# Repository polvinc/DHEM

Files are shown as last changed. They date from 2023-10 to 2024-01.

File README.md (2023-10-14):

# DHEM: another DIY Harmonic Equatorial Mount
## What the hell is this DHEM thing?

DHEM (DIY Harmonic Equatorial Mount) is an equatorial mount for observation or astrophotography. It is based on the use of a harmonic reducer. The mount is designed to be inexpensive in relation to its performance, transportable, with a relatively large load capacity. Most importantly, this mount is easy to build: no need for machine tools or other laser-cutting-water-jet-plasma-turbo-piston-5-axis machines. A shopping list, a screwdriver, a saw and some resourcefulness: you've got everything you need to make a DHEM. The ultimate aim is to distribute its design as an open-source product for personal use.

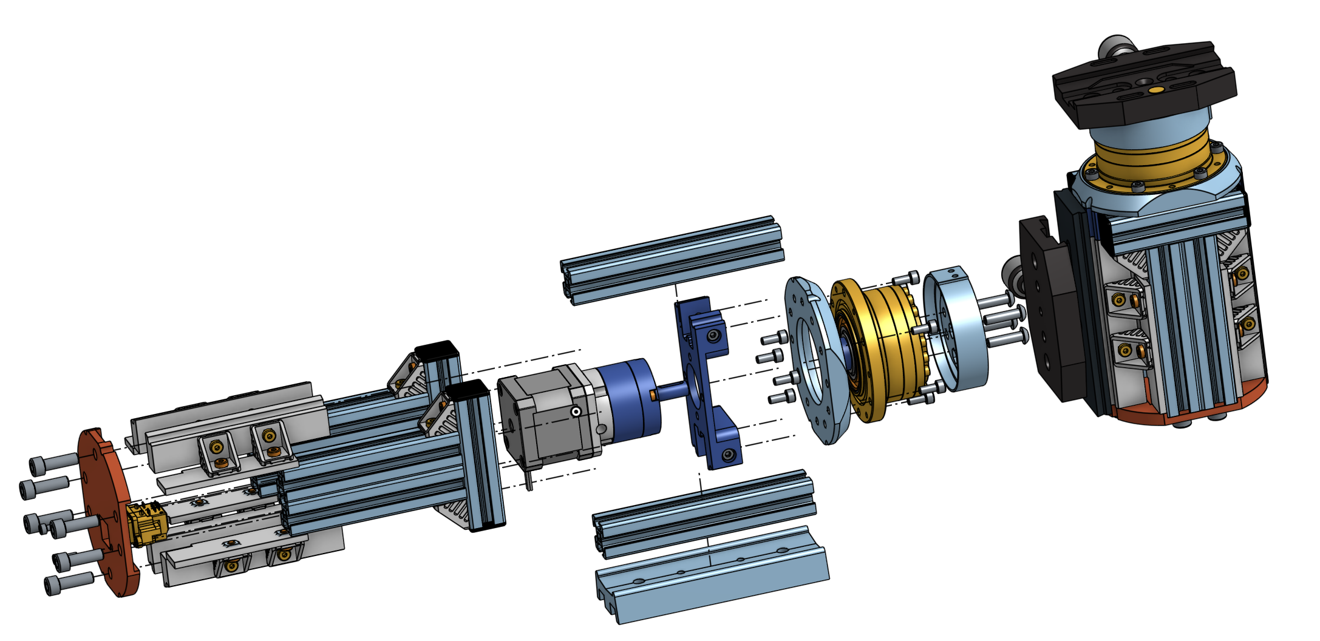
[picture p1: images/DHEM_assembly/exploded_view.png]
exploded_view


The technology used in this mount is similar to that used in robotics or industrial production lines. The main mechanical gearbox is a harmonic gearbox ([wikipedia](https://en.wikipedia.org/wiki/Strain_wave_gearing)). 



It can produce surprising results for an astronomical mount at first glance; the mount appears grossly undersized and unbalanced, whereas the whole assembly is extremely robust and stable, with enormous torque.
Conventional equatorial mounts require the use of counterweights. The aim of this development is to make available the design of a harmonic mount that can be built in your garage, with few tools or mechanical knowledge, for a price of less than 1000€. Of course, the proud aim is to achieve performance equivalent to that of commercial harmonic reduction mounts.

- Harmonic gear motor
- BOM less than 1000€
- No need for machine tools: all you need is a saw and a screwdriver!
- Lightweight: max 5 kg
- Minimum load weight without counterweight: > 12kg (to be tested)

The first results of the performance tests are up to my expectations for the moment. I hope this github repository can help you design or reproduce this equatorial mount. Please be patient, I'm only working on this project in my spare time. I'll update the testing progress on this readme. ✍️

## Support

Hey! Help me out for a couple of :beers: !

<a href="https://www.buymeacoffee.com/polvinc" target="_blank">Buy Me A Coffee</a>

# Design
## 3D design
The 3D design was carried out on SolidWorks 2022 and OnShape. Here's a [sharing of the design on OnShape](https://cad.onshape.com/documents/8746a60a1be674f3c5c8962f/w/75df6ccf1ddba0eb14d42c4d/e/8f9338159e7a1463ffcd3219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). The project is a bit of a mess, but it includes all the components needed to assemble the mount. You will find all stl files for printing in this repo.

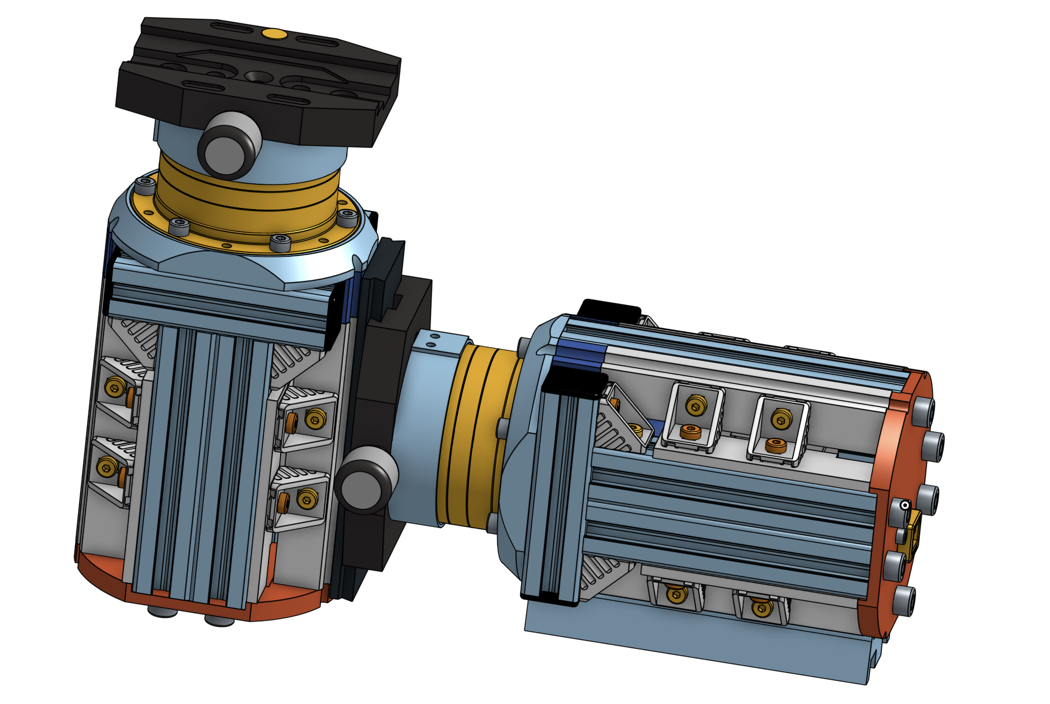
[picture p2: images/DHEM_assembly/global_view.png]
global_view


## Bill of materials
Here's the shopping list for two axes. Prices are approximate: I already had quite a few parts in stock when designing the DHEM. The total investment is around 900€ for the mechanics, and I estimate the cost of making an [OnStep](https://onstep.groups.io/g/main/wiki/Home) MiniPCB2 controller at 100€.

<b>The estimated total cost of the equatorial mount is less than 1000€</b>.

I think you can save a lot of money by going to other supply sites. For example, I got about €70 worth of Bosch M4 T-nuts from RS Components, when I could have got them for 5 or 10 times less with no-name ([for example](https://www.amazon.fr/EYPINS-Connecteur-Aluminium-28x28x20mm-dextrusion/dp/B08GPRB9W4/?th=1), [another example](https://www.amazon.fr/alwaiiz-aluminium-galvanisé-dextrusion-européenne/dp/B0B5GKW3MT/)). I had Bosch in my stuff, so I didn't deprive myself.

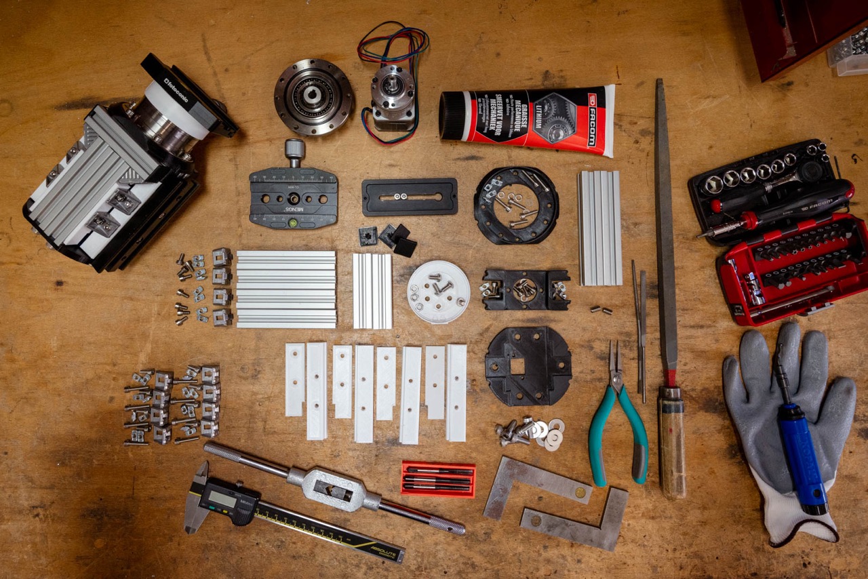
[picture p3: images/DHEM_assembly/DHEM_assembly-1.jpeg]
final_assembly_1


| Name | Quantity | Reference | Price € | Link |
| --- | --- | --- | --- | --- |
M4x8 | 32 | - | a few | 
M4x10 | 16 | - | a few | 
M4x16 | 20 | - | a few | 
M4x20 | 20 | - | a few | 
M5x10 | 8 | - | a few | 
M5x20 | 6 | - | a few | 
M6x16 | 12 | - | a few | 
20mm Bosch Rexroth profile | 1 | 212-3292 | 25 | [RS components](https://fr.rs-online.com/web/p/tubes-et-profiles-de-structures/2123292?gb=s)
T-nuts | 64 | 466-7281 | 70 | [RS components](https://fr.rs-online.com/web/p/raccords-pour-elements-de-structure/4667281)
M4 Angle Bracket | 24 | 180-9136 | 30 | [RS components](https://fr.rs-online.com/web/p/raccords-pour-elements-de-structure/1809136)
M4 inside M6 insert | 4 | B096VSWCBQ | 8 | [Amazon FR](https://www.amazon.fr/dp/B096VSWCBQ?psc=1&ref=ppx_yo2ov_dt_b_product_details)
Dovetail Clamp | 1 | EUF9144C | 30 | [Amazon FR](https://www.amazon.fr/gp/product/B08TC111QC/ref=ppx_yo_dt_b_search_asin_title?ie=UTF8&psc=1)
Dovetail Mounting Plate | 1 | EUF9175B | 20 | [Amazon FR](https://www.amazon.fr/gp/product/B08XLWP13X/ref=ppx_yo_dt_b_search_asin_title?ie=UTF8&psc=1)
Arca clamp | 1 | B0BW3SSHY1 | 20 | [Amazon FR](https://www.amazon.fr/QLOUNI-dégagement-Déclenchement-Appareil-Universelle/dp/B0BW3SSHY1/)
Arca mounting | 1 | B0771KW7TK | 15 | [Amazon FR](https://www.amazon.fr/gp/product/B0771KW7TK/ref=ppx_yo_dt_b_search_asin_title?ie=UTF8&th=1)
| Nema 17 with 10:1 Planetary Gearbox | 2 | 17HS15-1584S-MG10 | 60 | [StepperOnline](https://www.omc-stepperonline.com/fr/nema-17-moteur-pas-a-pas-l-40mm-rapport-de-vitesse-10-1-reducteur-planetaire-serie-mg-17hs15-1584s-mg10)
Harmonic Drive | 2 | CSF-17-100-2UH | 550 | [ebay](https://www.ebay.fr/sch/i.html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) ([datasheet](https://www.harmonicdrive.net/products/gear-units/gear-units/csf-2uh/csf-17-100-2uh))
RJ45 connector | 2 | MRJ5380M1 | 35 | [Farnell](https://fr.farnell.com/amphenol-communications-solutions/mrj5380m1/conn-rj45-90-jack-8p8c-1-port/dp/4122450)
OnStep controller | 1 | MiniPCB2 | ~100 | [oshwlab](https://oshwlab.com/hujer.roman/minipcb2)

# Assembly

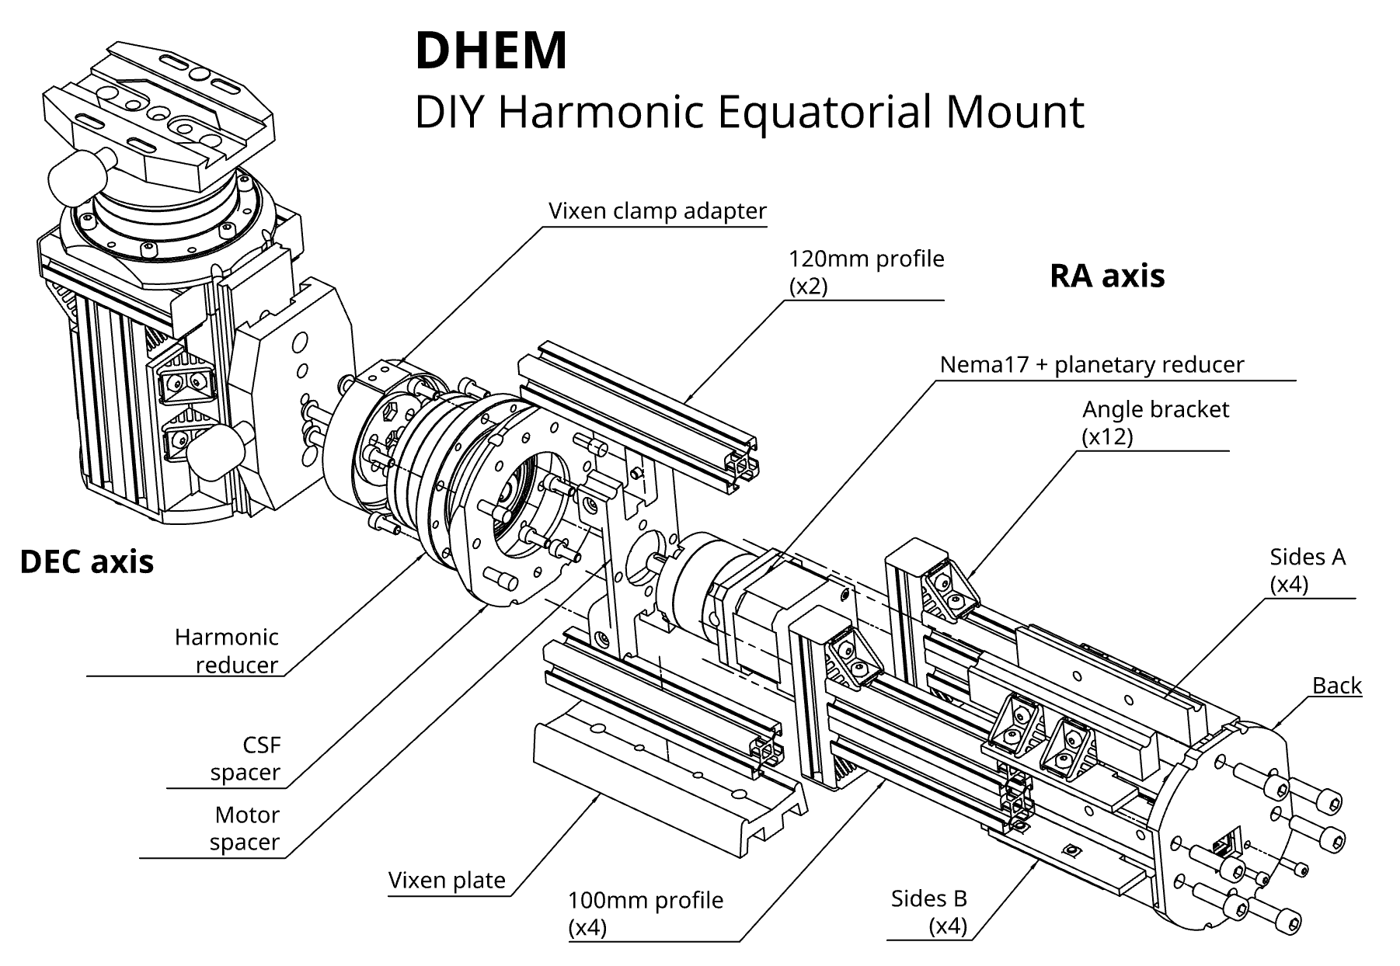
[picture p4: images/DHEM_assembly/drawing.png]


## Harmonic drive
Harmonic gearboxes ([wikipedia](https://en.wikipedia.org/wiki/Strain_wave_gearing)), or more precisely strain wave gears, are a type of gear mechanism that transmits much more torque than other common gears. This is mainly due to the fact that there are many more teeth engaged at once. One of the major advantages of these gears is that they have virtually no backlash, partly because they use deformation. It's a bit like belts, which are supposed to be more or less backlash-free, but harmonic gearboxes use deformable metal spring steels, which are much better than belts.

Put another way, in the case of an astronomical mount: they can drive much heavier loads without the need for counterweights, all with a very low self-weight!

<p align="center">
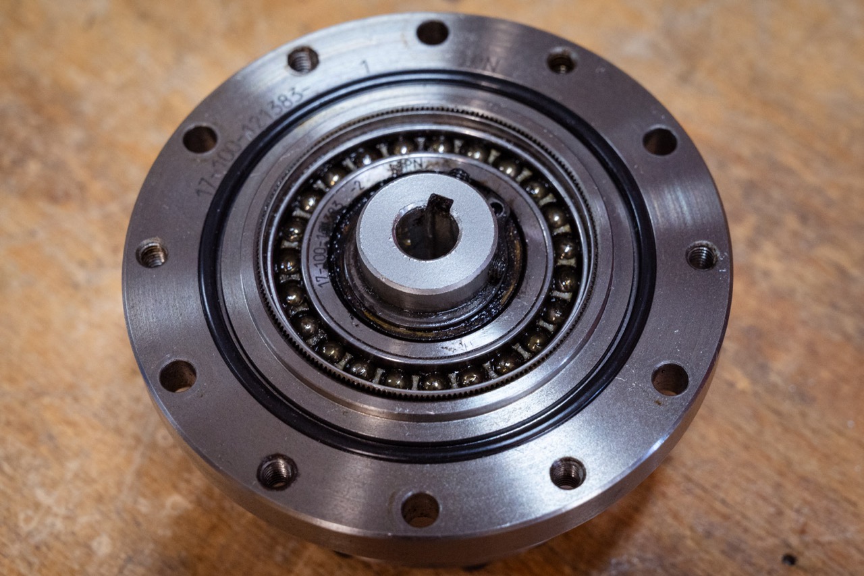
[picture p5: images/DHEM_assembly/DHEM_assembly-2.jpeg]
  
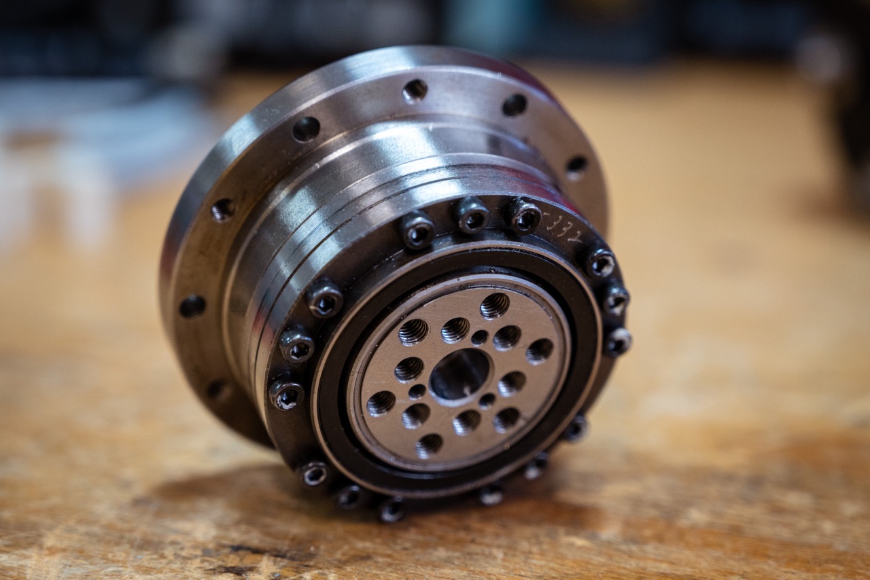
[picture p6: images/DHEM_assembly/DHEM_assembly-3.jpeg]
  
</p> 

The harmonic reducer model chosen [CSF-17-100-2UH](https://harmonicdrive.de/fileadmin/user_upload/Harmonic_Drive_Gears_EN_1050860_06_2022.pdf#page=50) is the same as [Alan](https://alanz.info/posts/2022/07/diy-mount/) DIY mount. You can find lots of them on ebay. This one has a reduction ratio of 1/100. It has the good fortune to meet my requirements, and to have been tested for another equatorial mount. Why deprive yourself? According to datasheet, it can handle more than 50Nm of torque and it also has a very comfortable permissible radial load of over 70Kg.
<p align="center">
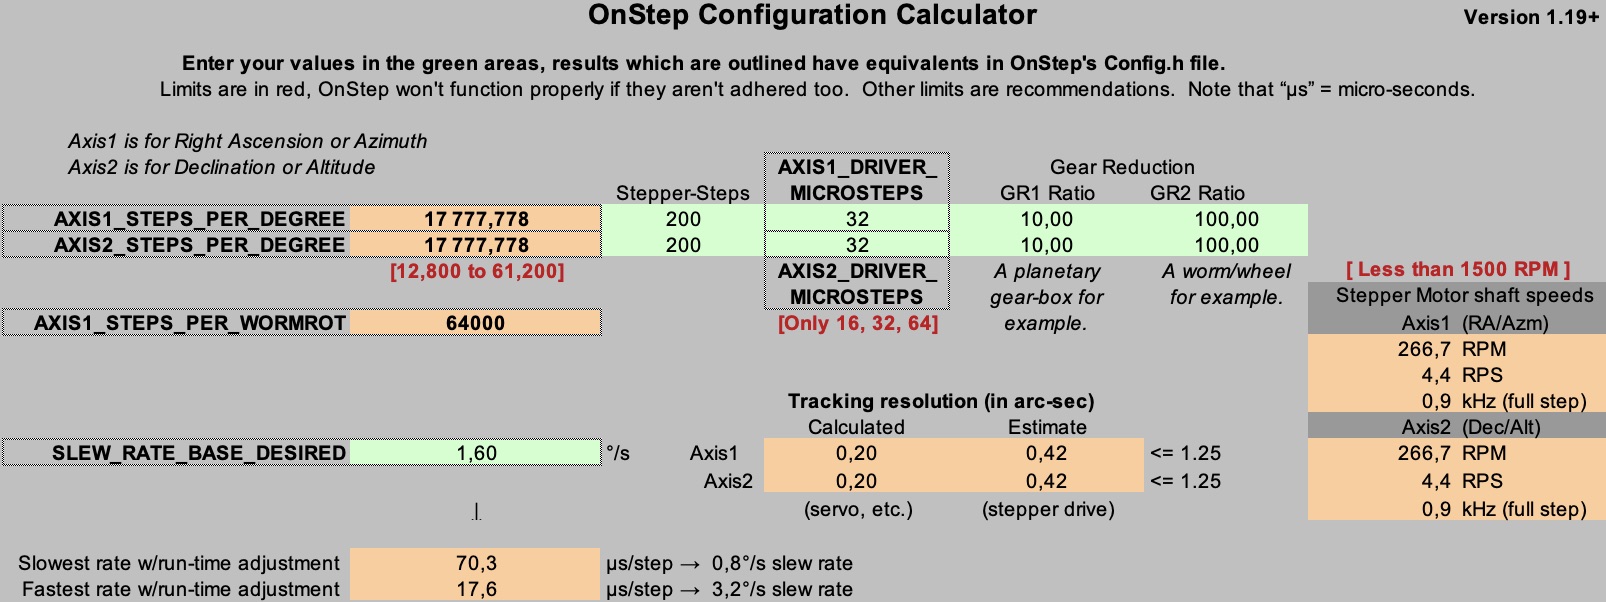
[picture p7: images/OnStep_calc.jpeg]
  
</p>

Using [OnStep's configurator spreadsheet](http://o.baheyeldin.com:1111), I chose to drive the harmonic gearbox with a planetary gearbox [17HS15-1584S-MG10](https://www.omc-stepperonline.com/fr/nema-17-moteur-pas-a-pas-l-40mm-rapport-de-vitesse-10-1-reducteur-planetaire-serie-mg-17hs15-1584s-mg10), in order to achieve good tracking resolution, a good slew rate and a good number of steps/deg. Its reduction ratio is 1/10 and it is given for a low backlash (around 30 arcmin). Seen through the telescope, this low backlash will be divided by 100 by the main gearbox. You can probably use another motor with a planetary gearbox.

<p align="center">
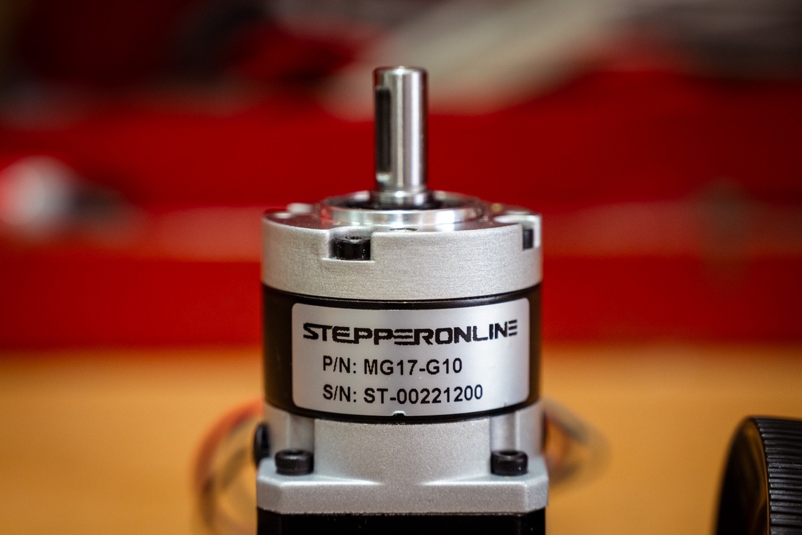
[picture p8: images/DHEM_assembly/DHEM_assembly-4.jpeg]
  
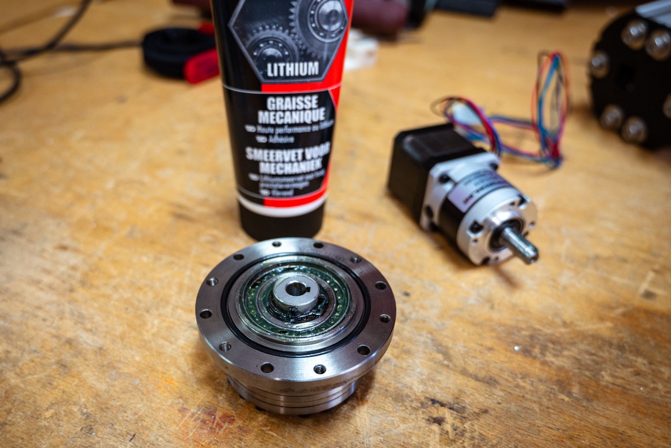
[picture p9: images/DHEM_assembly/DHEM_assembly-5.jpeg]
  
</p>

## Motor holding
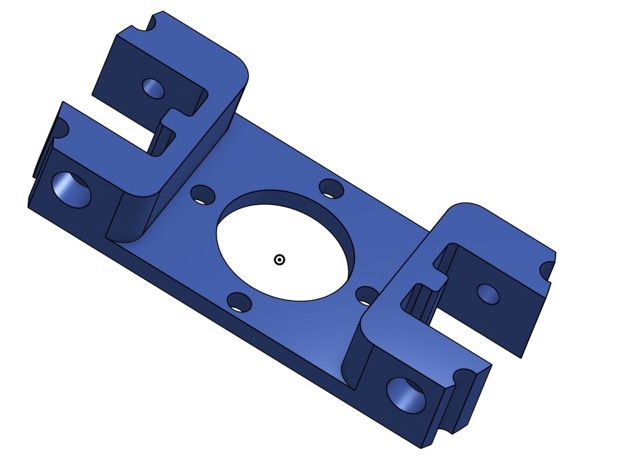
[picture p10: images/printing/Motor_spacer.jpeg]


We start assembling the mount, attaching the motor and its planet gear to the 3D-printed motor spacer with M4 screws. I printed most of my parts in PETG or ABS, with an Ultimaker S7, in 0.15mm layers, slow speed, high infill, and 101% flow.
Two 20mm Bosch Rexroth profile bars are cut at 120mm, and tapped on both sides with M6. An M6 (external) to M4 (internal) insert is housed on one side of the two Rexroths. These two bars are then positioned in their housings, and secured with 4 T-nuts. The M6/M4 insert is located on the motor shaft side. It will be used to attach the assembly to the harmonic gearbox. Note the orientation of the Nema 17 motor in relation to the two 120mm bars. The motor wires must be oriented in the space available on the bar side.

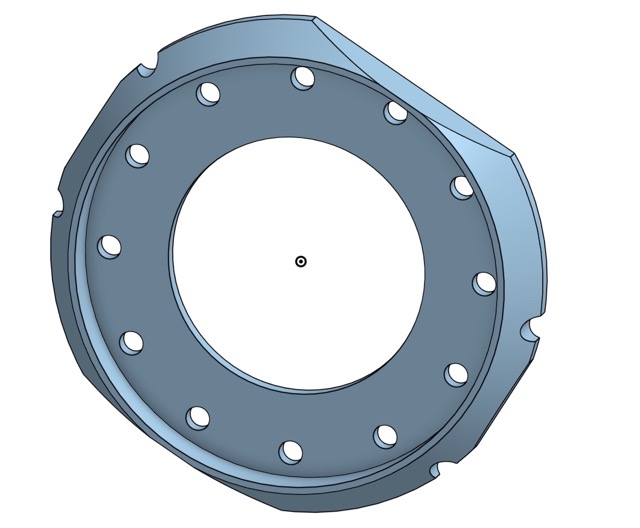
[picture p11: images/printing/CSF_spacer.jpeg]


Once the CSF spacer has been centered on the harmonic gearbox, the assembly is secured to the gearbox using two M4 screws. Make sure you fit your 2 M4 screws into two plain holes in the gearbox flange. Do not use the tapped holes (every other hole is plain).
Don't forget to insert the key on the motor shaft, and secure the shaft in the harmonic gearbox with the two M3 set screws. Make sure that the bars are properly aligned, perpendicular to the bearing plane on the harmonic gearbox.

As can be seen from the images, the 3D printed motor spacer has no major structural function. It provides a few degrees of flexibility between the planetary gearbox shaft and the harmonic gearbox bore. Its only structural function is to hold and space the motor, with only a degree of rigidity on the torque transmission. So it's no big deal that this part is 3D printed and not made of metal. Once again, however, take care to print the parts properly.

<p align="center">
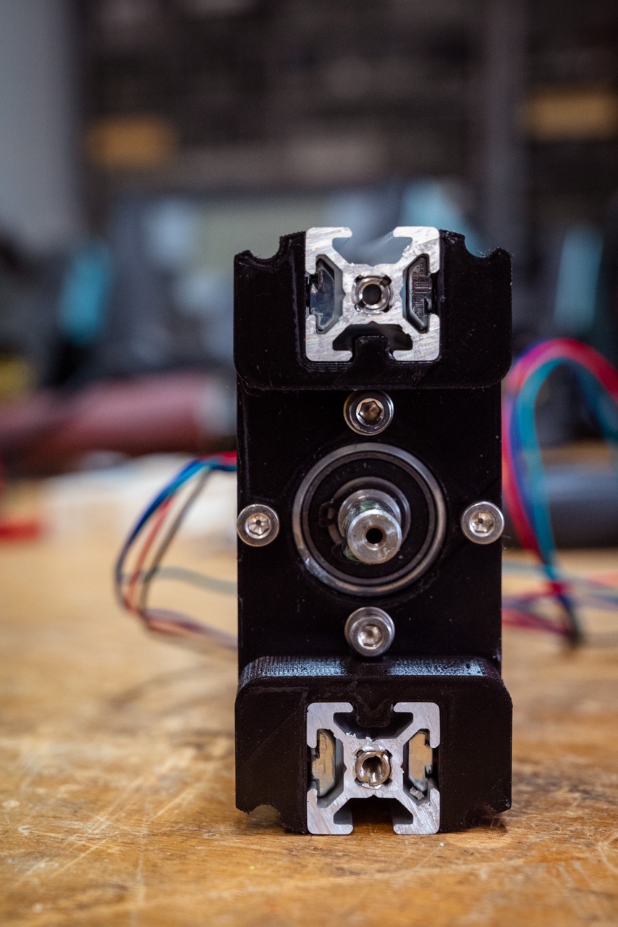
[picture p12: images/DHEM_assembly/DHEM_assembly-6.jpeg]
  
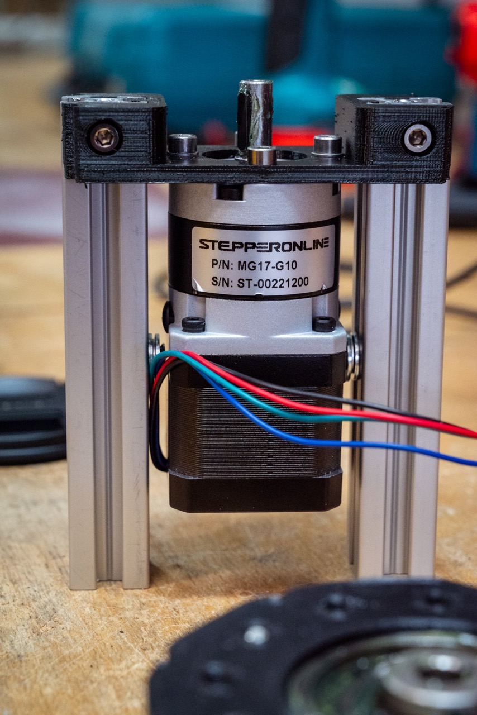
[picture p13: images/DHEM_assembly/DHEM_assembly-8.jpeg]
  
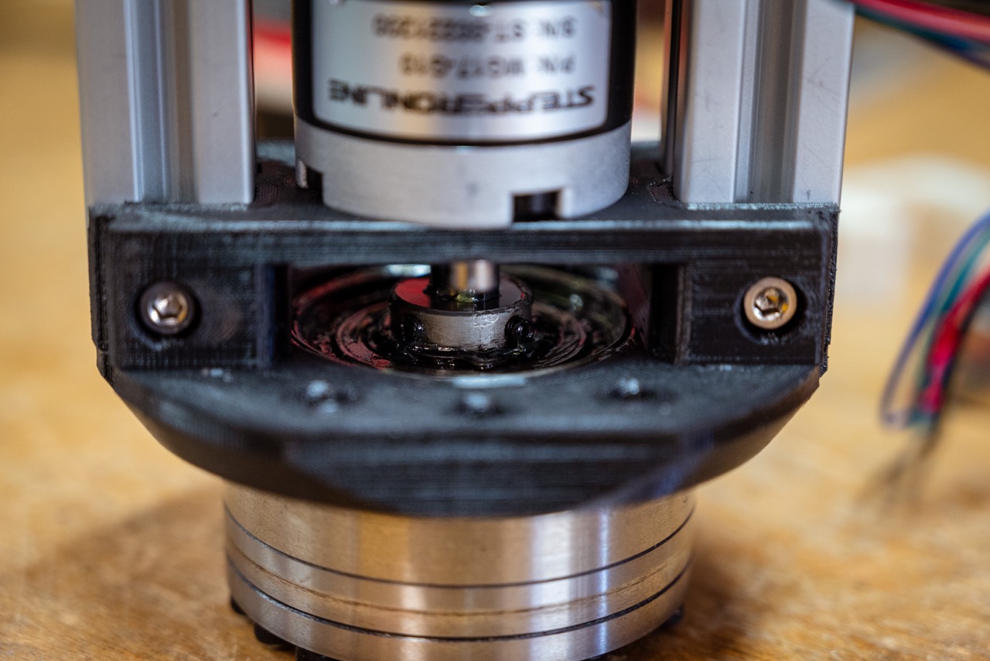
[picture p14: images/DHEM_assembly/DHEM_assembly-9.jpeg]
  
</p>

## Sides Rex
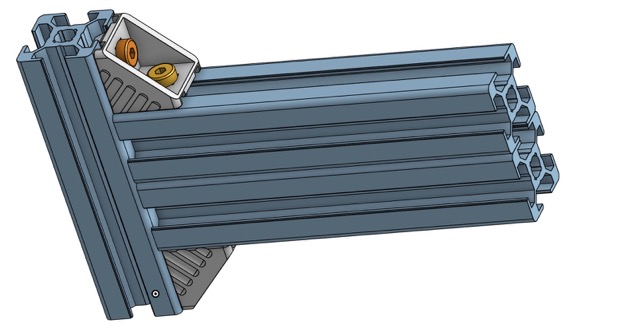
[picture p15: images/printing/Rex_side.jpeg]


To assemble the frame sides, first cut two 76mm bars and four 100mm bars. You could also use 2 Bosch Rexroth [20 x 40 mm aluminium profiles](https://fr.rs-online.com/web/p/tubes-et-profiles-de-structures/2123294?gb=s), cut to 100mm. The 100mm bars are M6 tapped on one side. These threads will be used to secure the frame's back plate. Prepare 4 angle brackets with M4 and T-nuts.

<p align="center">
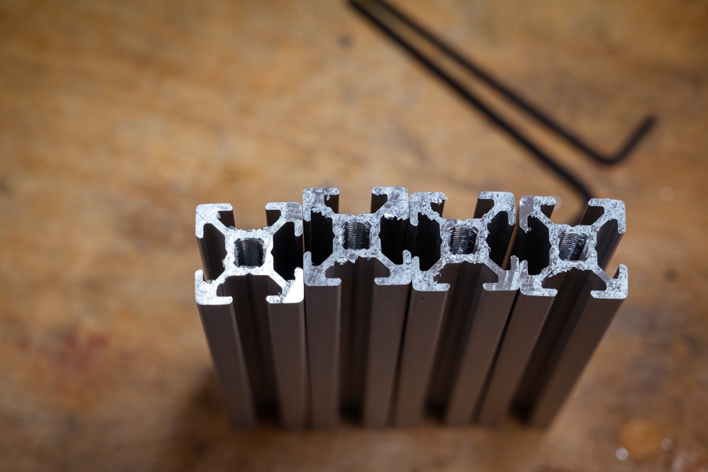
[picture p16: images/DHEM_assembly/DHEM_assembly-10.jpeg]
  
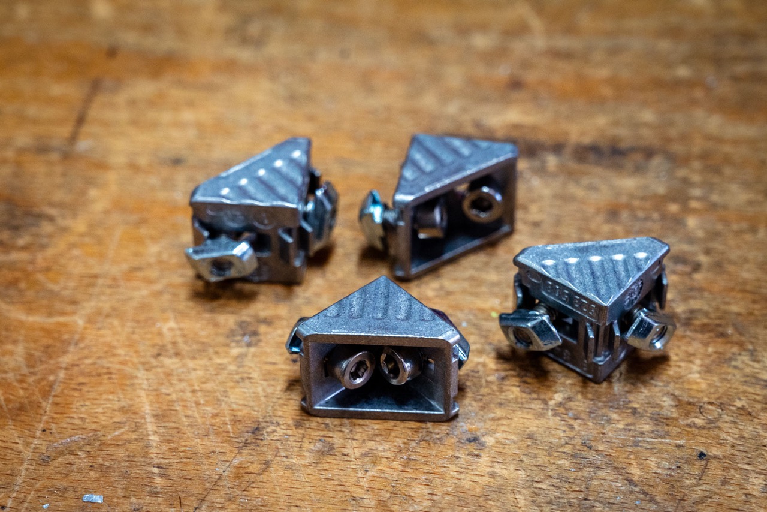
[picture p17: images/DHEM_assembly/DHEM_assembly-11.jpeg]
  
</p> 

Assemble with M4 T-nuts and four squares as shown in the pictures. Take care to ensure that the T-nuts are correctly seated in the grooves of the Rexroth bars.

<p align="center">
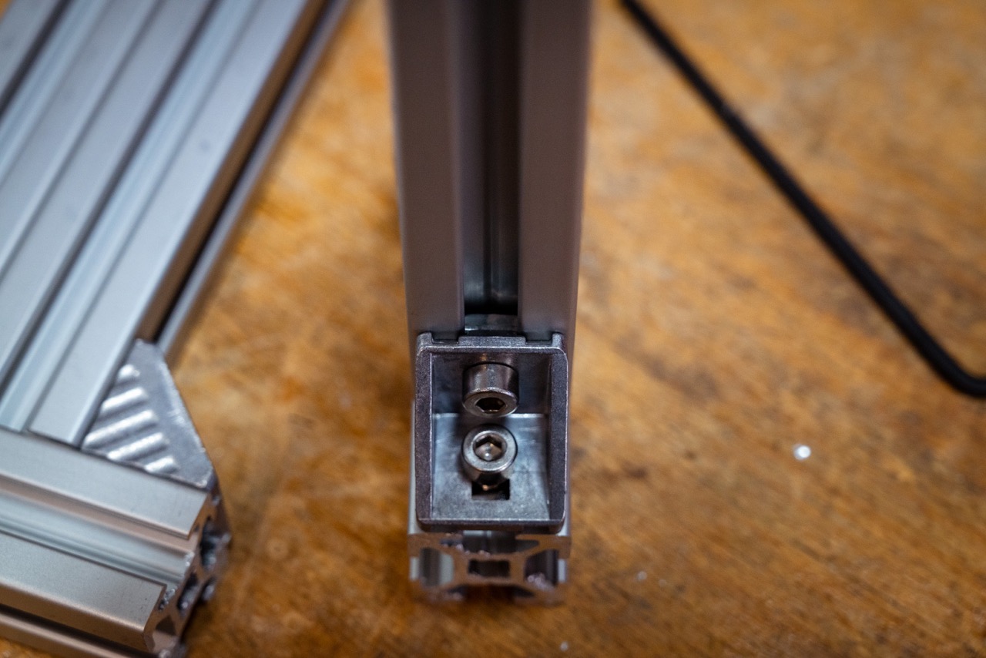
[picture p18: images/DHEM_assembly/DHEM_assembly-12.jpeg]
  
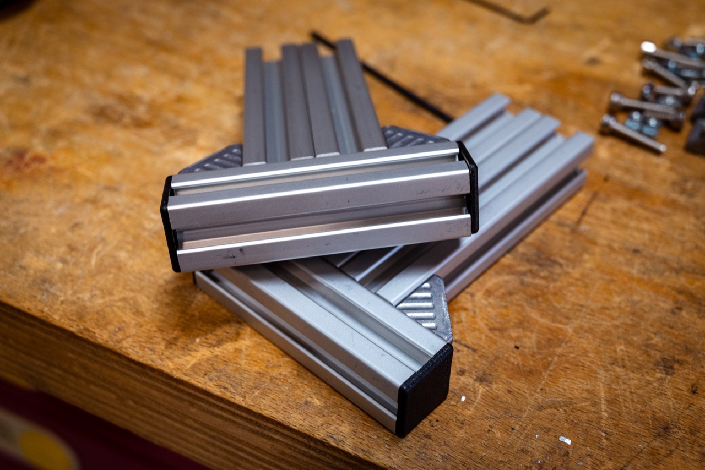
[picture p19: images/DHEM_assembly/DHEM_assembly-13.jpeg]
  
</p>

The next step is to assemble the sides on the harmonic reducer. The harmonic reducer is always the reference point for perpendicularity. Fixing is achieved with 4 M4 screws and 4 T-nuts.

<p align="center">
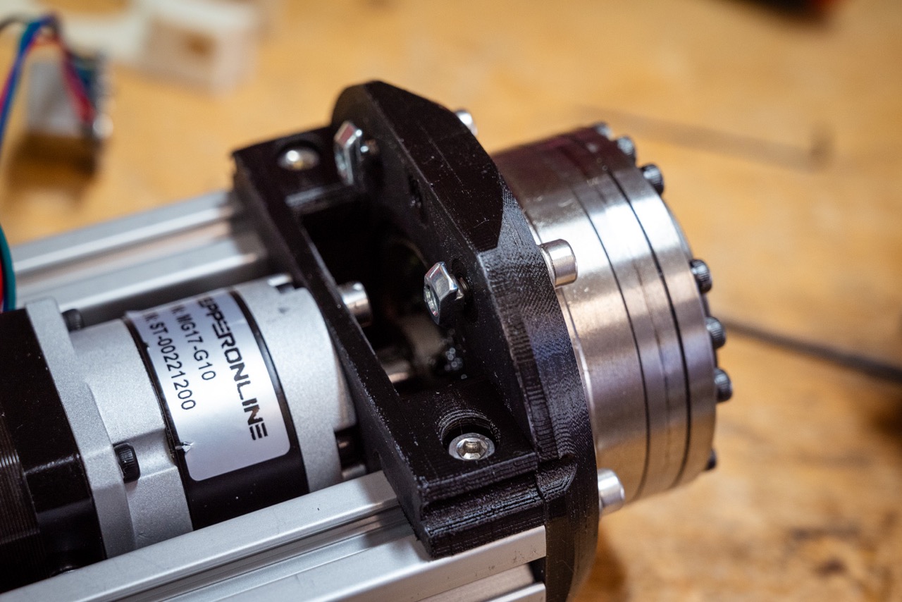
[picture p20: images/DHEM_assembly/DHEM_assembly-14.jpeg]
  
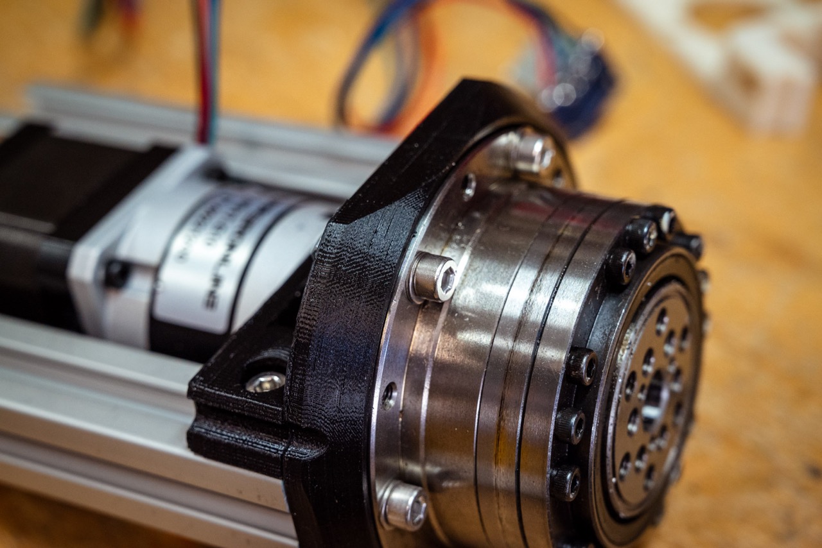
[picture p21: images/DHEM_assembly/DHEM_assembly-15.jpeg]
  
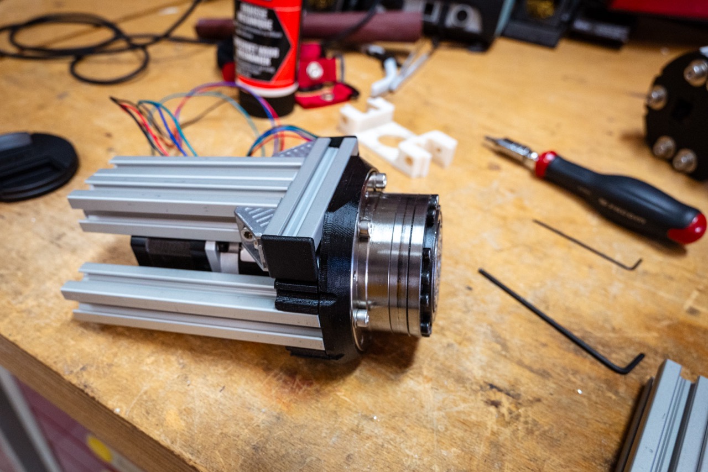
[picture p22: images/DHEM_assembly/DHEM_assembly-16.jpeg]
  
</p> 

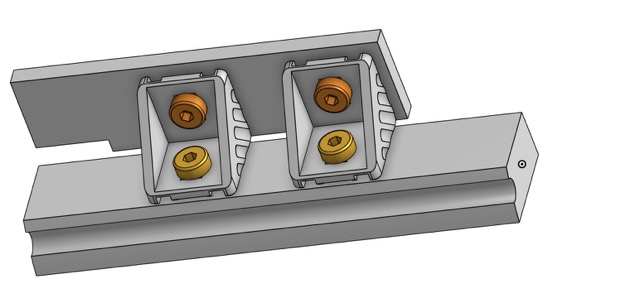
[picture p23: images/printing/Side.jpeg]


Now it's time to position the frame blanks, using the two printed supports to bridge the gap between the brackets and the bars. Take care to align the brackets with the Rexroths already in place, mainly for aesthetic reasons, but also for the future attachment of the dovetail/arca mounting plates. There are a couple of parts to be printed four times, and oriented correctly along the aluminium profile sides. The most important thing in this part of the assembly is to properly secure the T-nuts in the profile. The screws compress the 3D-printed spacers, so there's no risk of weakening the structure.

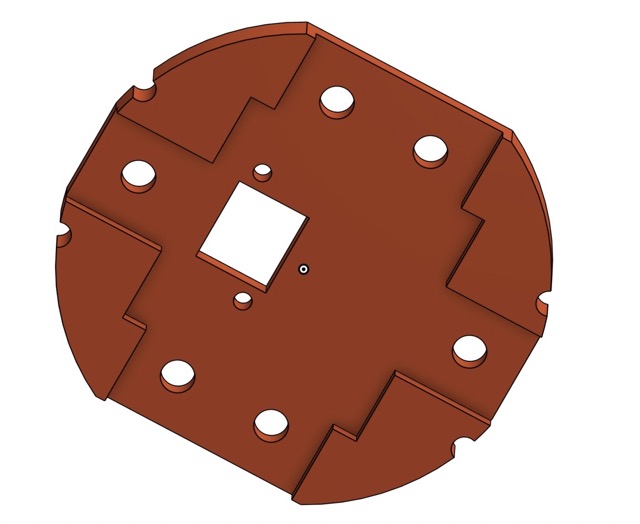
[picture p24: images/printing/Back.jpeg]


Finally, secure the bottom plate with 6 M6 screws and washers. When you've done this, you can check that your Rexroths are correctly aligned. Beforehand, you can attach the ethernet connector to the back plate with M3, after soldering the motor cable to it. I chose the MRJ5380M1 because my OnStep comes out in RJ45 and I had some in stock, but it is not necessarily the cheapest of the RJ45 connectors. You may need to modify this part if you choose a different RJ45 or other connector.

You have almost finished assembling a DHEM axis!

<p align="center">
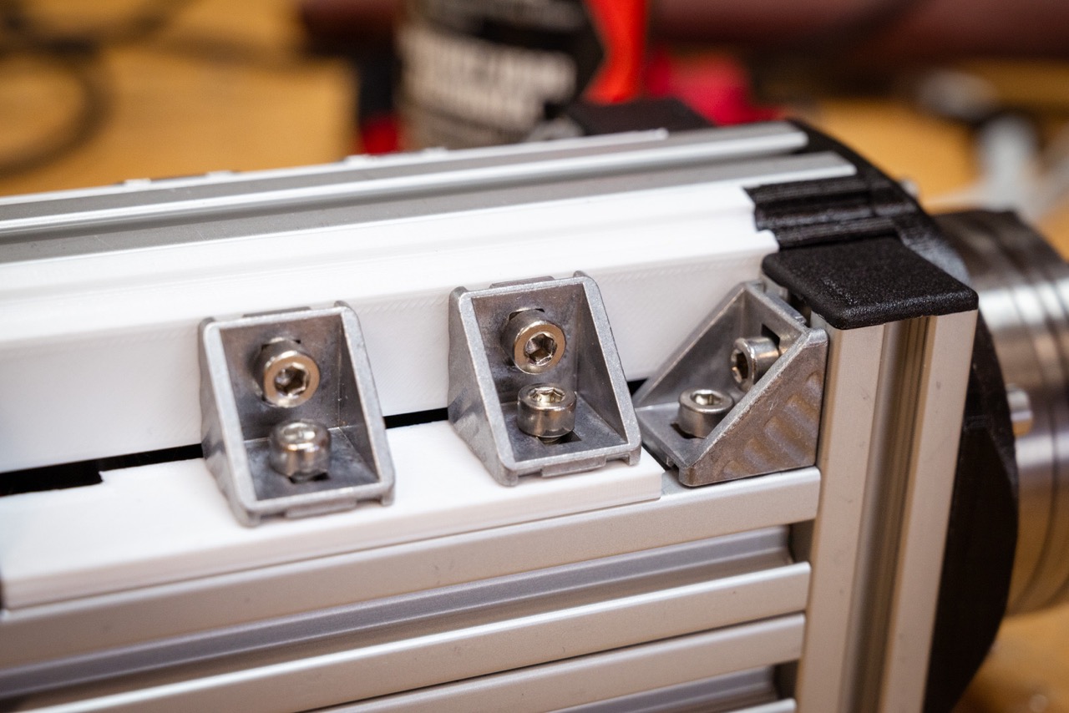
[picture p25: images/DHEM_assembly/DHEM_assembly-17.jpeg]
  
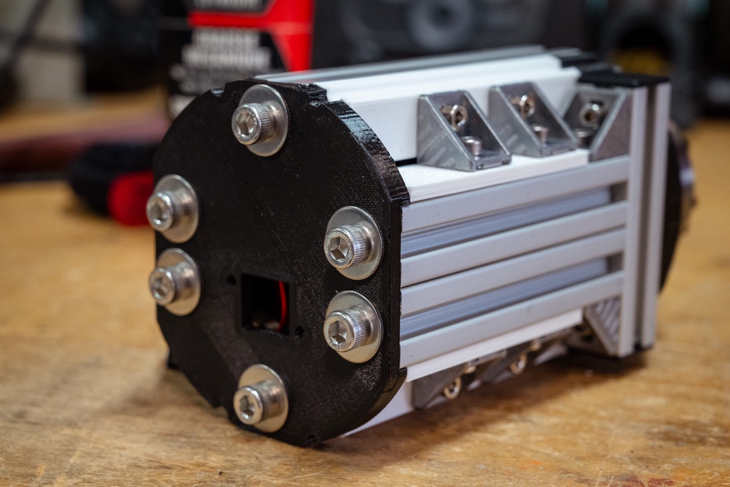
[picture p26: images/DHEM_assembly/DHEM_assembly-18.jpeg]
  
</p>

## Vixen/Arca mount
All that remains is to attach the adapter rings for your dovetail/arca clamp. I also made a plate from a block of aluminum, which seemed more rigid to me during the carrying mass tests. It's up to you to design your vixen clamp adapter if you don't choose the BOM one. I've made two versions: an arca swiss one for photo lenses, and a vixen one for telescopes.
<p align="center">
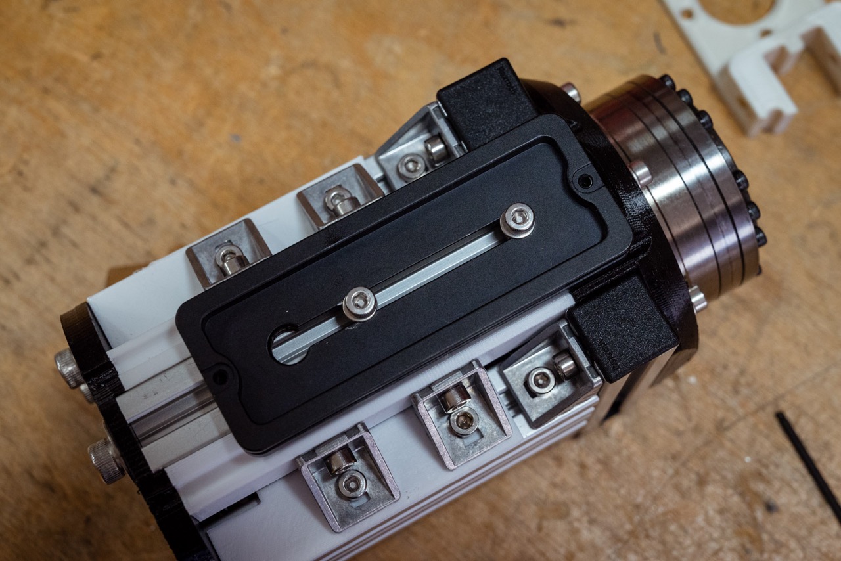
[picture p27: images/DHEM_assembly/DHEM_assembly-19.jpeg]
  
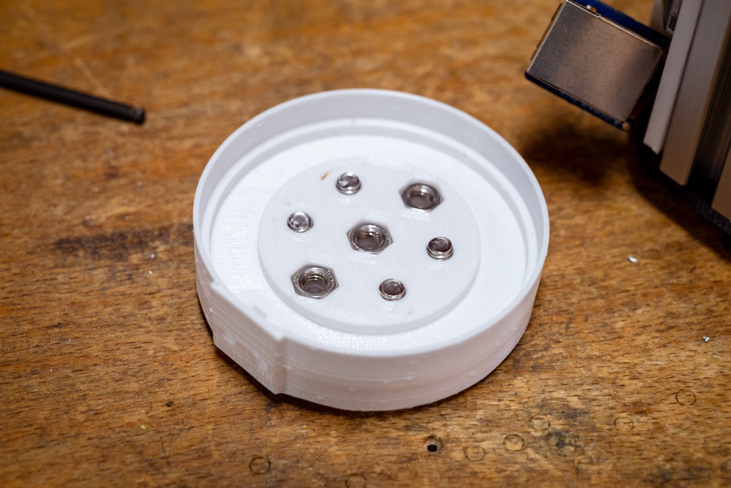
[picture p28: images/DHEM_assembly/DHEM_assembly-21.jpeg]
  
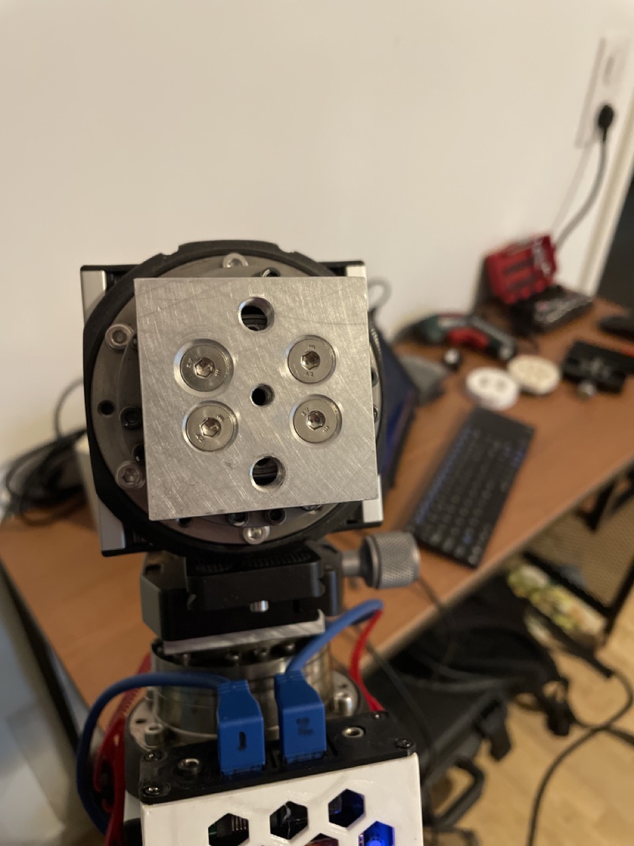
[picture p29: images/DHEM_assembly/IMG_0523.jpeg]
  
</p>

## Final assembly
<p align="center">
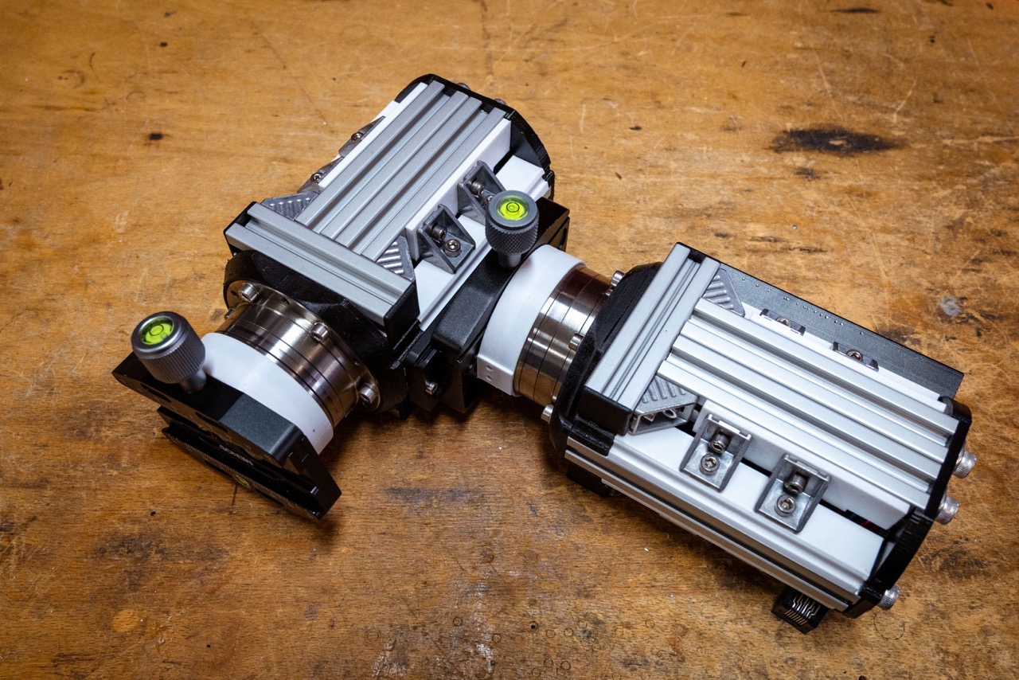
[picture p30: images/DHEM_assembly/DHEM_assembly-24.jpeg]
  
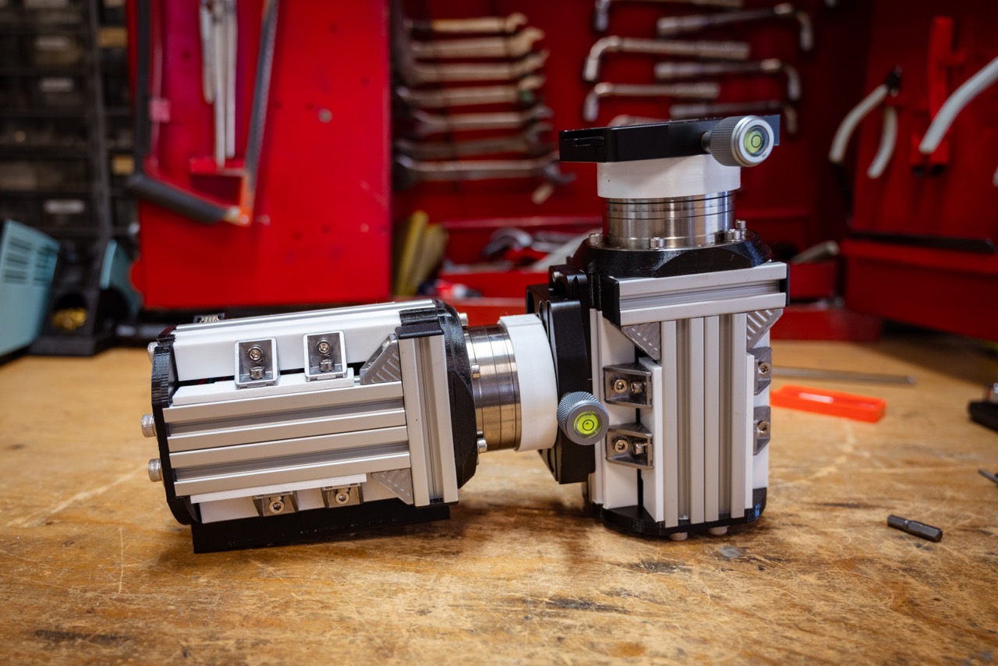
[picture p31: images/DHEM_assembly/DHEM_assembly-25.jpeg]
  
</p>

I had in stock a small equatorial table (Omegon 55mm) on which I put the mount. In the future, I plan to design a Rexroth-based equatorial table wich fits with the DHEM.
<p align="center">
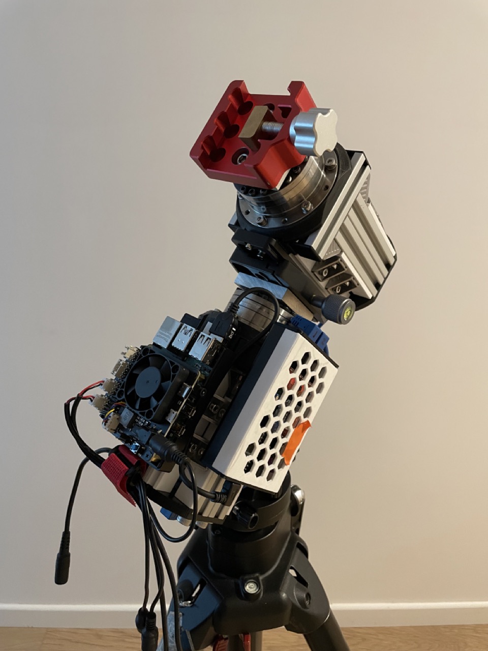
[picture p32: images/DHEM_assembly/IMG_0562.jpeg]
  
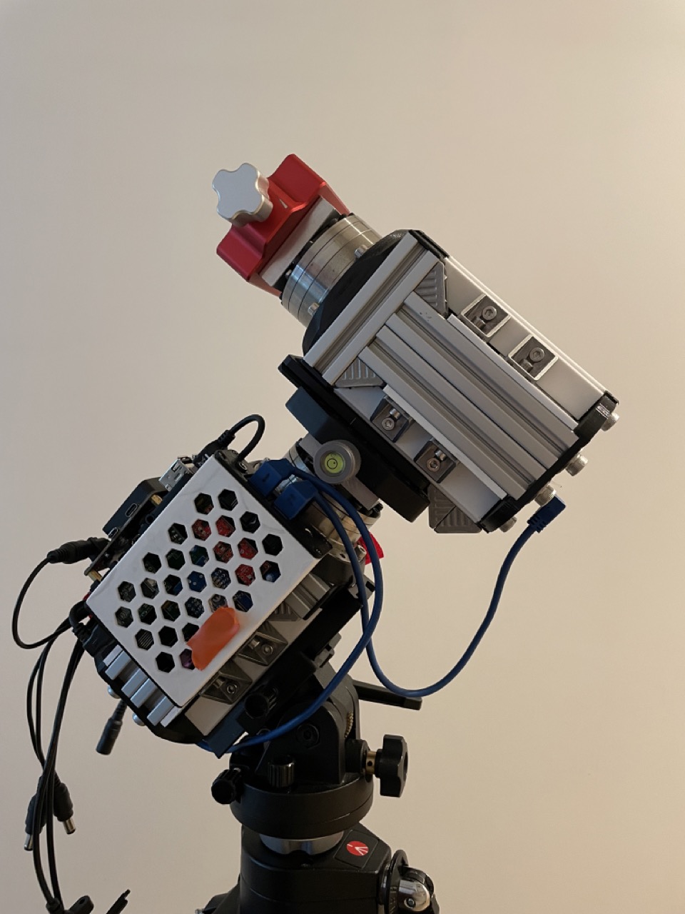
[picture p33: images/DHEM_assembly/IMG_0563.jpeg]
  
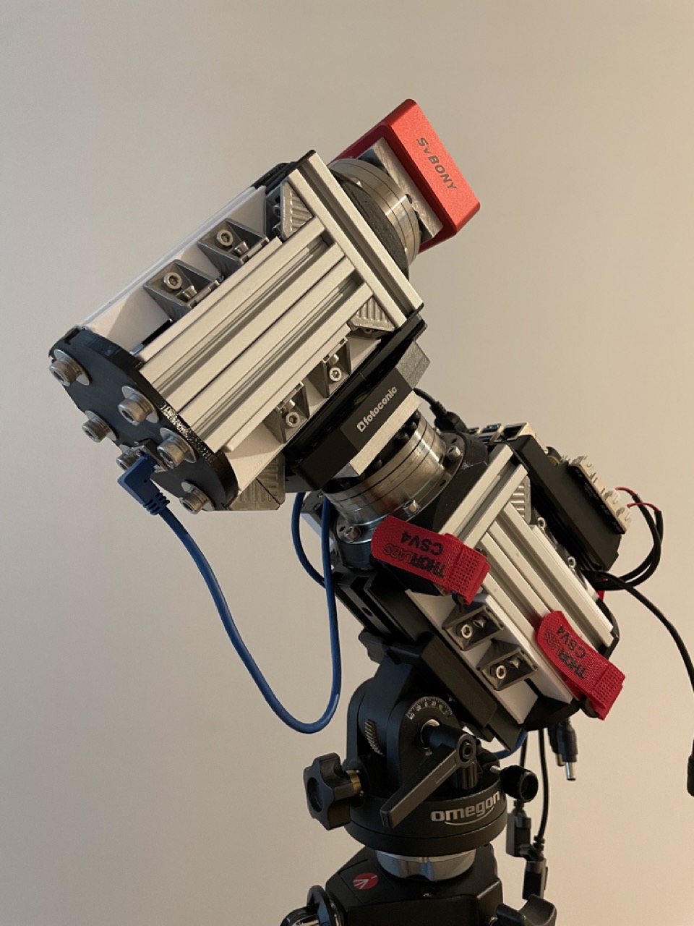
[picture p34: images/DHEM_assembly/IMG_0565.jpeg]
  
</p> 

# Tests
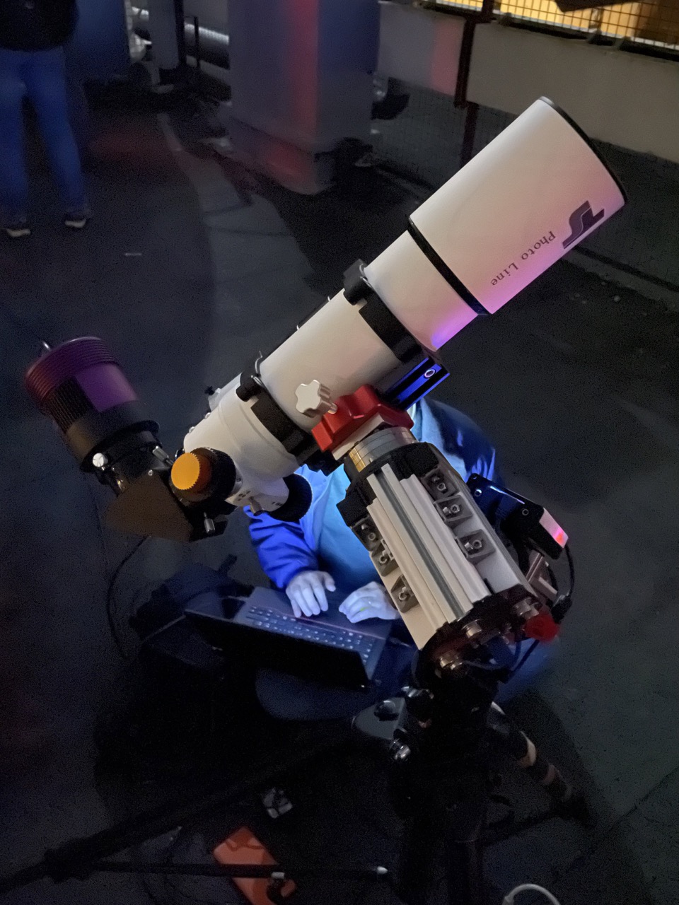
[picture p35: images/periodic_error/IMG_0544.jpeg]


- ✍️ Work still in progress
- [Vélizy astronomy club](https://www.astro-velizy.fr/)
- First tests
- Strategy
- Astrophoto
- Mount capacity
- Mechanics
- Electronics
- Software

## Periodic error measurements
One way to measure the mount's periodic error is to derange its polar alignment by 5-10°, point at a star in the celestial equator zone, set the mount to tracking (it thinks it's compensating for the earth's rotation when it's misaligned), and let a star drift in the field for a while. By stacking the images of this star's drift, we can observe an image of the periodic error pattern. If the star drift is perfectly linear, the mount has no periodic error. If, on the other hand, the star drift follows a sinusoidal pattern, then we observe a periodic error due to the mechanics of the mount. Pixel measurements are then used to quantify the error.

Radians are converted to arcsec as: <b>1 rad = 3600 x 180 / pi = 206264.81 arcsec</b>. 
Resolution in arcsec per pixel can then be calculated as follows: 
<p align="center">
  <b>pixel[µm] x 206264.81[arcsec] / (1000 x focal)[µm] = [arcsec/pixel]</b>
</p>

In this test, I used a 480mm focal length and a CCD with 4.93µm pixel size (thanks to [Vélizy astronomy club](https://www.astro-velizy.fr/)). This gives an image resolution of around 2.12"/px. Below is a stacked image of approximately 30min of exposure (180 exposures of 10sec). The telescope was pointing at Altair. We could take into account the correction linked to the choice of star: Altair is at 8°57' apparent declination. We therefore need to multiply the amplitude by 1.012 (or forget this correction, as we're talking about a 1% error).
<p align="center">
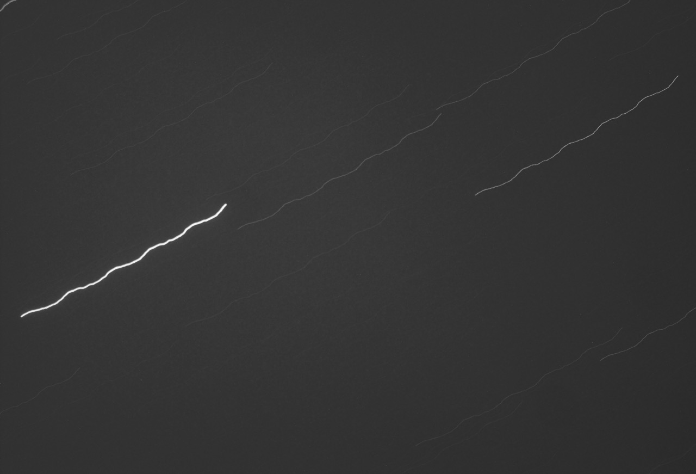
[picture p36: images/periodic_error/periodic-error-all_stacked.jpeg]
  
</p>

Then, I take a few pixel measurements with Python help (source: [guiqwt](https://github.com/PlotPyStack/guiqwt)).

```python
import os.path as osp
from guiqwt.plot import ImageDialog
from guiqwt.tools import AnnotatedSegmentTool, AnnotatedPointTool, XCursorTool
from guiqwt.builder import make

def window():
    win = ImageDialog(toolbar=True, wintitle="PEC")
    for toolklass in (XCursorTool, AnnotatedSegmentTool, AnnotatedPointTool):
        win.add_tool(toolklass)
    return win

def app():
    import guidata
    _app = guidata.qapplication()
    fn = osp.join(osp.dirname(__file__), 'periodic-error-all_stacked.jpeg')
    win = window()
    image = make.image(filename=fn, colormap="bone")
    plot = win.get_plot()
    plot.add_item(image)
    win.exec_()

if __name__ == "__main__":
    app()
```

<p align="center">
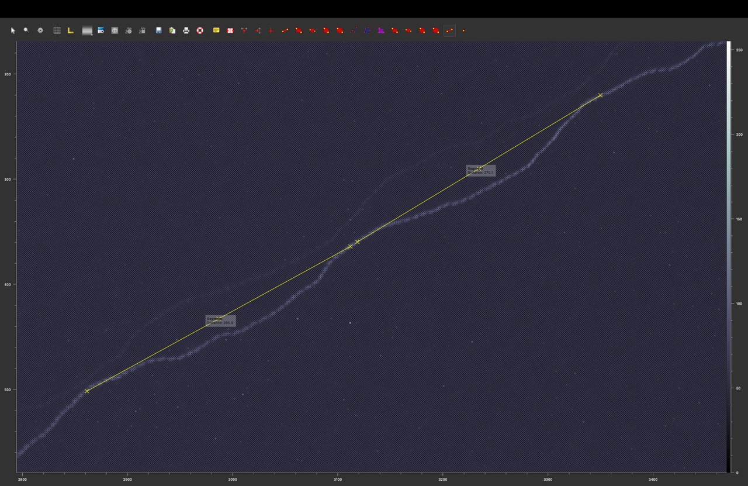
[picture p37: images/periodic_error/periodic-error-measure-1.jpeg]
  
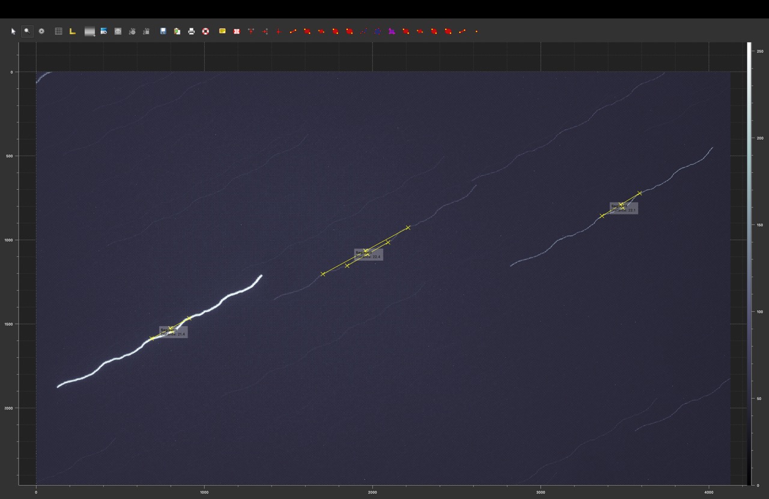
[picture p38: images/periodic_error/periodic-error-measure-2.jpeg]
  
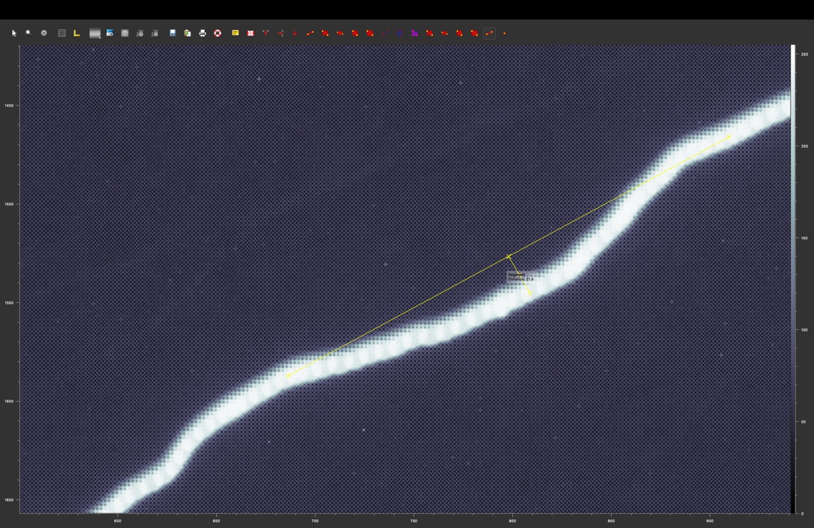
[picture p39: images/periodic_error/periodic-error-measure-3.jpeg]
  
</p> <p align="center">
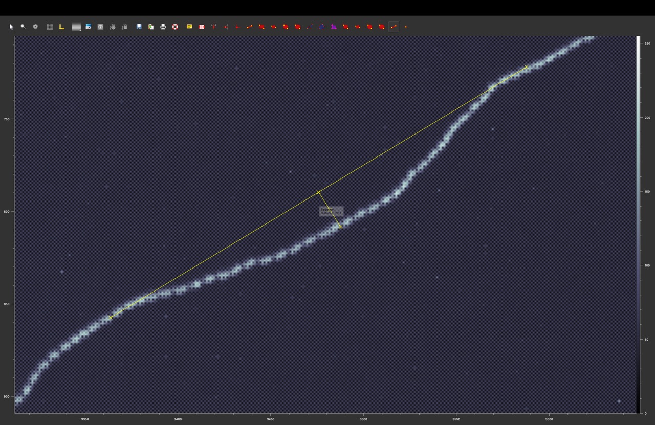
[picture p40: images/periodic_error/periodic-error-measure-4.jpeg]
  
  
  
</p>

I measure about 22px peak-to-peak amplitude, i.e. <b>about ±23" periodic error</b>. 

The periodic error of harmonic gears is naturally greater than that of worm gears. This is mainly due to the fact that the pitch circle of the gear is relatively small. The datasheet also provides a precision <1.5 arcmin, i.e. 90arcsec.
Self-guidance is therefore necessary for photography, and unguided photography is possible using short focal length lenses and/or short exposure. The ripple is smooth, with no hard points. The period is long compared with the few seconds of integration required with a guiding camera.

If I dare to compare with commercially available harmonic mount, I can see that we're in the right order of magnitude. For example, for the ZWO AM5, many different values can be found on the Internet, but the order of magnitude of the periodic error seems to be around ±20" ([ZWO](https://astronomy-imaging-camera.com/tutorials/10-things-you-need-to-know-about-the-custom-am5s-pe-test-report-provided-by-zwo/)). For the Rainbow Astro RST-135, it's about ±30" ([Rainbow Astro](https://www.rainbowastro.com/faq-eng/#:~:text=We%20don%27t%20make%20an,length%20lenses%20and%20short%20exposure)).

The sequence of 180 images was produced between 23h34m17s and 00h11m10s, i.e. 36.9min. The stacked image shows about 5 periods of oscillation. From this, we can deduce the duration of an oscillation period to be approximately 7.4min. The measured period is therefore <b>approximately 440 seconds</b>. In fact, if we look at the operation of a harmonic gearbox, the wave generator (attached to input shaft) produces a rotation of 100 turns per 360 degrees on the output shaft. For each revolution of the wave generator, we have twice the period of the potential periodic error. We can deduce the theoretical period of the periodic error equal to (24x60x60)/(2x100)=432sec. We're pretty close to what we roughly measure on the stacked image, which is reassuring! We can assume that the period is somewhere around these two values. Only the training of a self-guidance model will be able to tell.

## Guiding performances

[Good article on harmonic mount, periodic error and guiding](https://bbs.astronomy-imaging-camera.com/d/15989-getting-the-best-performance-from-my-am5)
[NASA](https://articles.adsabs.harvard.edu//full/1991NASCP3113..237N/0000241.000.html)

## Next step: analysis of dynamic guiding behavior
- How does Onstep+DHEM behave when correction pulses are sent by INDI commands?
- How does the mechanics behave in terms of inertia, torque and increase in on-board mass (with or without counterweight)?? 
- What is the impact of the small mechanical play on the declination axis during correction pulses (tilting moment stiffness = 18.6 Nm/arcmin)?
- Take a picture !
- Comparison with AM5 and EQ6-R
- And so on !

# About me
I'm a novice in astronomy or astrophotography, but I've been coding and making stuff, among other things for photography, for over 15 years now. I am a scientist, an expert in infrasound sensors, which has nothing to do with astrophotography, but above all I am eager for new challenges. Even though I don't have a telescope (for the moment, only a few pro DSLR cameras and telephoto lenses), about 2 years ago, in my free time, I set out this design.

To help me in my task, I have drawn on the work of several sources. I can't mention them all, but I'd like to thank the work of [Roman Hujer](https://github.com/romanhujer/HrEM) and [Kenichi Aihara](https://mr-deep-addicted.com/?page_id=1770), who introduced me to the benefits of a harmonic reducer for an equatorial mount using 3D printing. For the design I wanted to create, I had to limit machining and parts with adjustment. To achieve this, I designed the robot with a direct axial drive. As my work progressed, I discovered [Alan Zhao](https://alanz.info/posts/2022/07/diy-mount/)'s impressive work, and drew inspiration from it.

I must also mention the [Onstep](http://onstep.groups.io/) project, an extraordinary DIY electronics project that makes the design of a goto astronomical mount accessible. 

I've already designed or built several robots for automated photo-taking. These were either made from designs sourced from various online designers, or were self-designed. I'm only sharing the current version, the DHEM equatorial mount, which is clearly the most accomplished.
<p align="center">
  
  
  
  
</p> 

The first results of the performance tests are up to my expectations for the moment. I hope this github repository can help you design or reproduce this equatorial mount. Please be patient, I'm only working on this project in my spare time. I'll update the testing progress on this readme. ✍️

# Thanks
Many thanks to the [Vélizy astronomy club](https://www.astro-velizy.fr/) (Paris region in France), and its very helpful members, for the advice, the loan of equipment, the time spent testing, and the encouragement in this mount project.

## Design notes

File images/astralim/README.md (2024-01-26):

# AstrAlim board
## Open-source project
[link to the pcb design](https://oshwlab.com/pololamag/nafa-astralim)

Designed for amateur astronomers and built in conjunction with the hardware solution [NAFA-Hardware](https://github.com/dragonlost/NAFABox-hardware) (Nomad Astronomy For All), **AstrAlim** is a purpose-built add-on for the Raspberry Pi 5 or 4 mini-computer, specifically crafted to handle the electrical aspects of astrophotography sessions. This all-in-one HAT (Hardware Attached on Top) delivers the following features:
- **A single 12V DC, 15A input** in XT30 format streamlines power supply for the entire photo session, reducing complications and friction during telescope movement. It includes polarity protection.
- **A 5V, 5A power supply** to energize the Raspberry Pi.
- **Three controllable (ON/OFF) 12V DC outputs**, up to 36W, in DC Jack 2.1x5.5mm format for cameras, focusers, and filter wheels. One of these outputs allows selectable voltage between 12V, 9V, or 5V. Each output has current measurement via an INA219, and a self-resetting fuse secures the outgoing current up to 3A.
- **Two 12V PWM outputs**, up to 36W, in RCA/Cinch format to power up to two dew heaters, controllable to adjust their respective power levels. Current for each of these two outputs is also measured by an INA219, and a self-resetting fuse secures the outgoing current up to 3A.
- **Five red LEDs** provide visual feedback on the status of different outputs.
- **Two 1-wire outputs** and **two I2C outputs** for triggering and adjusting dew heaters based on the local dew point, by connecting temperature and humidity sensors, or other functions requiring these buses. ESD protection is included on these 4 outputs.
- **A 5-pin female header** for a NEO-6M Mini GPS module, with PPS (Pulse Per Second) output wired to the Raspberry Pi, providing precise time and positioning for nomadic astrophotography sessions, as well as the accuracy needed for occultation measurements.
- **A 32kbits EEPROM** ensures the Raspberry Pi recognizes AstrAlim at startup and initiates the necessary scripts for its proper functioning.
- **A 2x2p female direct-out connector** for future developments, allowing another stacked HAT to retrieve 12V voltage.

In summary, with the Raspberry Pi 5, **AstrAlim** offers a reliable, flexible, powerful, and energy-efficient solution, ideal for both fixed installations and nomadic use. This card also enables you to forgot conventional and costly proprietary systems, providing all the functions you might need to capture your most stunning pictures.

The software is currently being developed and fine-tuned.

A few statistics: 4 layers, 131 components, 1.7m track length, 97 vias, 446 pads, 48 resistors, 26 capacitors, 5 transistors, 5 MOSFETs, 5 polyfuses, 5 LEDs...



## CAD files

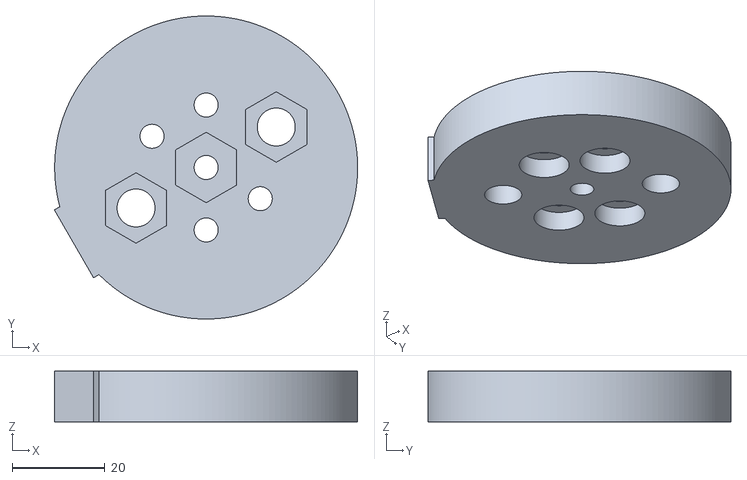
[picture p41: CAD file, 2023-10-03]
stl/Spacer_Vixen.stl
65.6 x 65.5 x 11.0

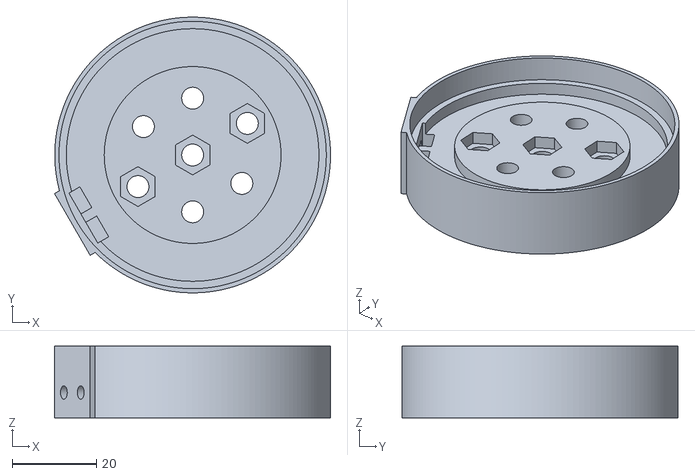
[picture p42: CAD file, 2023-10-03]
stl/Spacer_Arca.stl
65.6 x 65.5 x 17.0

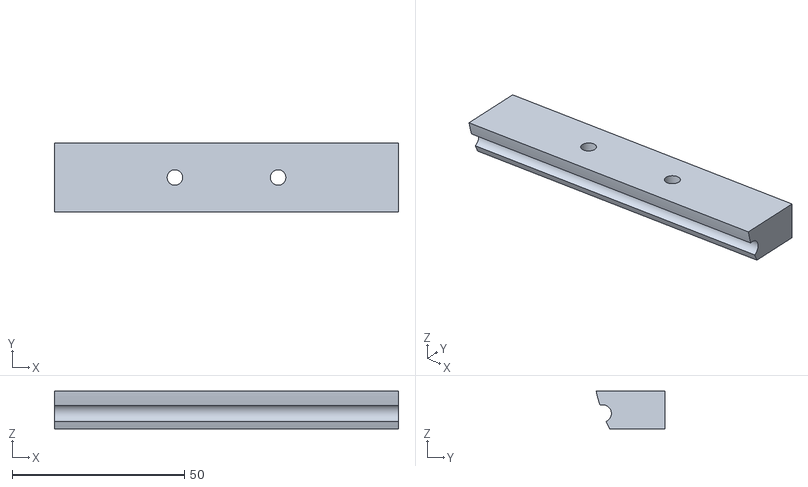
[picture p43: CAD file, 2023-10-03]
stl/Spacer_Bracket.stl
100.0 x 20.0 x 11.0

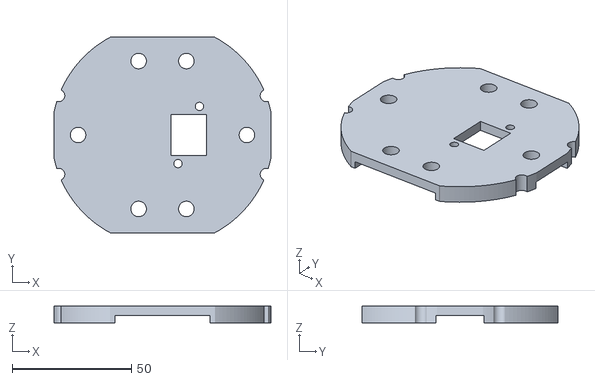
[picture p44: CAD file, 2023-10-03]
stl/Back.stl
91.0 x 82.0 x 7.00

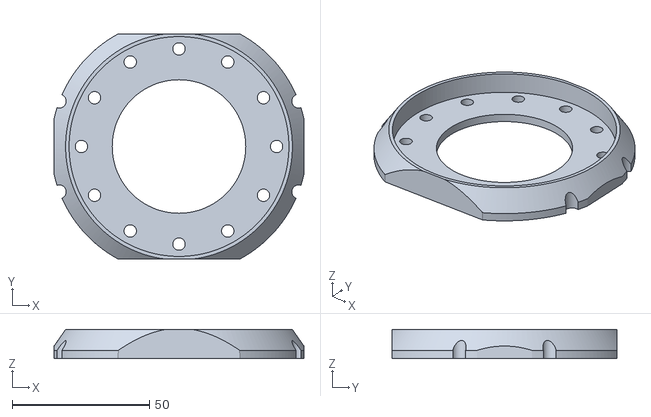
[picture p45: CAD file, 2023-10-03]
stl/Spacer_CSF.stl
91.0 x 82.0 x 10.6

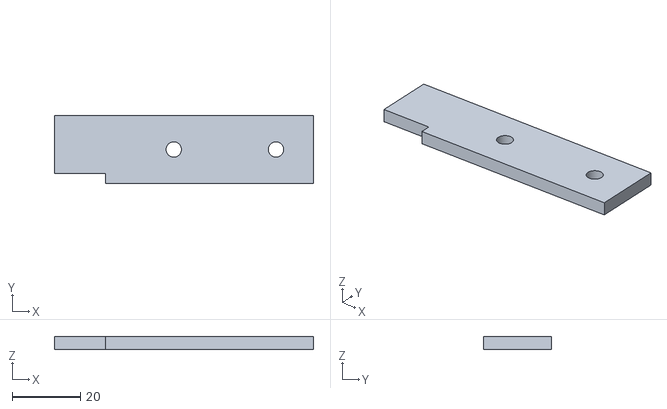
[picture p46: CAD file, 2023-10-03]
stl/Spacer_Bracket_2.stl
76.0 x 20.0 x 3.70

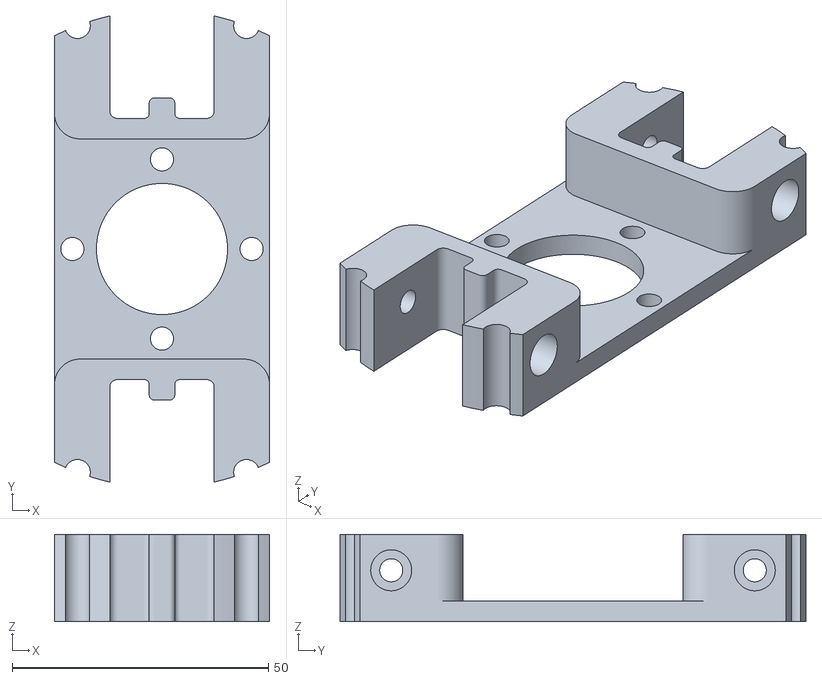
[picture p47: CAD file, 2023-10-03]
stl/Spacer_Motor.stl
42.0 x 91.0 x 17.0

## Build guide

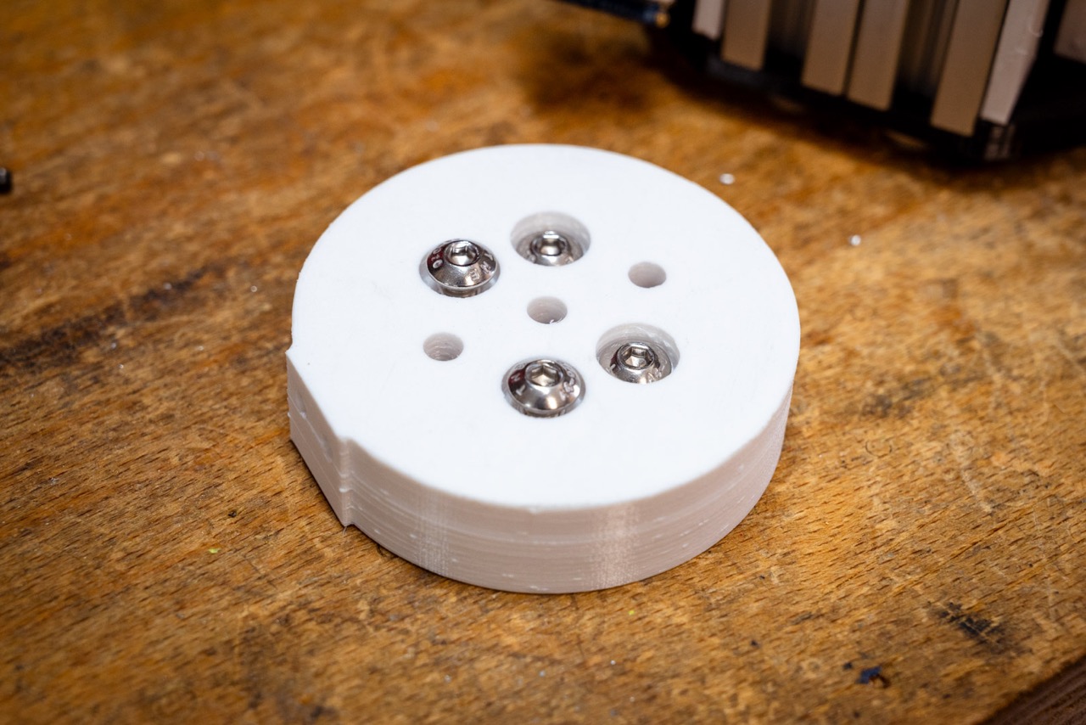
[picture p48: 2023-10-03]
images/DHEM_assembly/DHEM_assembly-20.jpeg
